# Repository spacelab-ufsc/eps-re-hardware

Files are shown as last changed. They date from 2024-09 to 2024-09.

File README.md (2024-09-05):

<h1 align="center">
	RELIABILITY ENHANCED ELECTRICAL POWER SYSTEM (RE²PS) HARDWARE
	<br>
</h1>

<p align="center">
    
    
    
    
    
    
</p>

<details>
    <summary><b>Summary</b></summary>
    <ol>
        <li>
            <a href="#overview">Overview</a>
        </li>
        <li>
            <a href="#repository-organization">Repository Organization</a>
        </li>
        <li>
            <a href="#license">License</a>
        </li>
        <li>
            <a href="#releases">Releases</a>
        </li>
        <li>
            <a href="#notes">Notes</a>
        </li>
        <li>
            <a href="#references">References</a>
        </li>
    </ol>
</details>

## Overview
The PCB of **RE²PS** [[1]](#1) was designed to be more reliable than previous EPS models developed by SpaceLab. To achieve this, ECSS standards for PCB development in space environments were tailored for the project [[2]](#2). Some flexibility was applied in selecting new connectors for interfacing with other modules, but whenever possible, previously used connectors, such as Pico-Locks and PicoBlades, were chosen.

<!-- 
<p align="center">
    <img src="https://github.com/spacelab-ufsc/eps-re-hardware/blob/main/outputs/eps-re_2D_top.svg" width="400"><img src="https://github.com/spacelab-ufsc/eps-re-hardware/blob/main/outputs/eps-re_2D_bottom.svg" width="400">
</p>
-->

<p align="center">
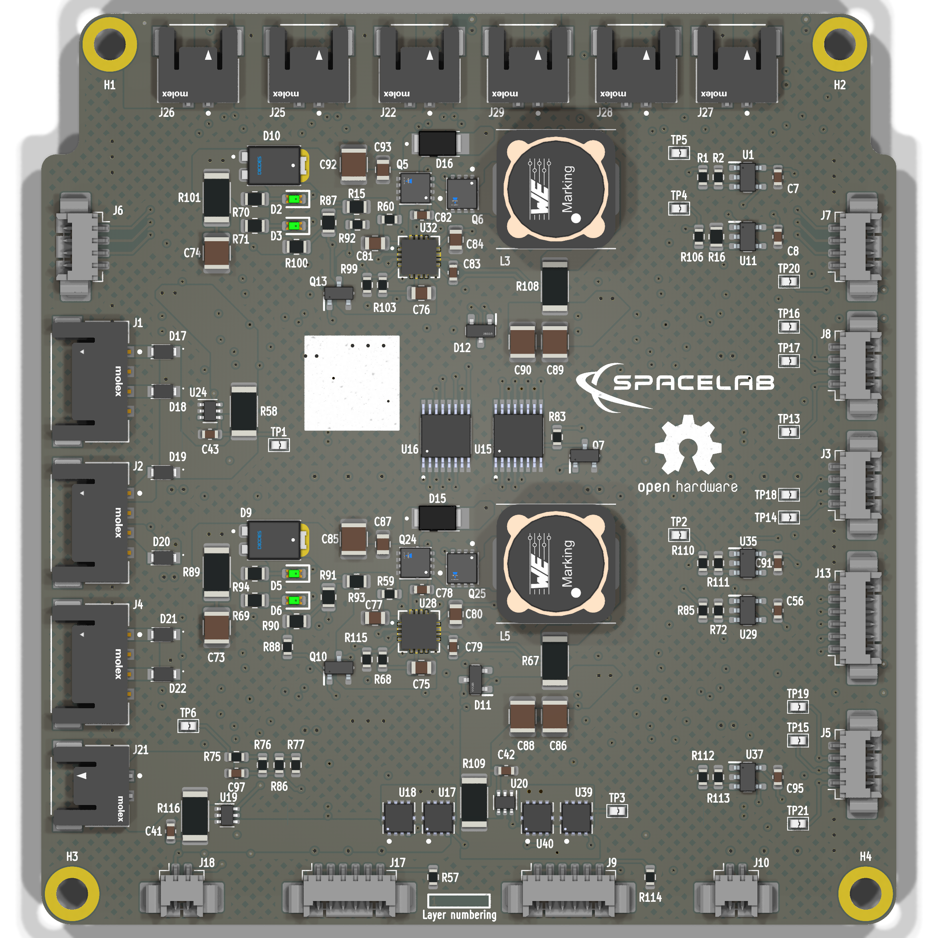
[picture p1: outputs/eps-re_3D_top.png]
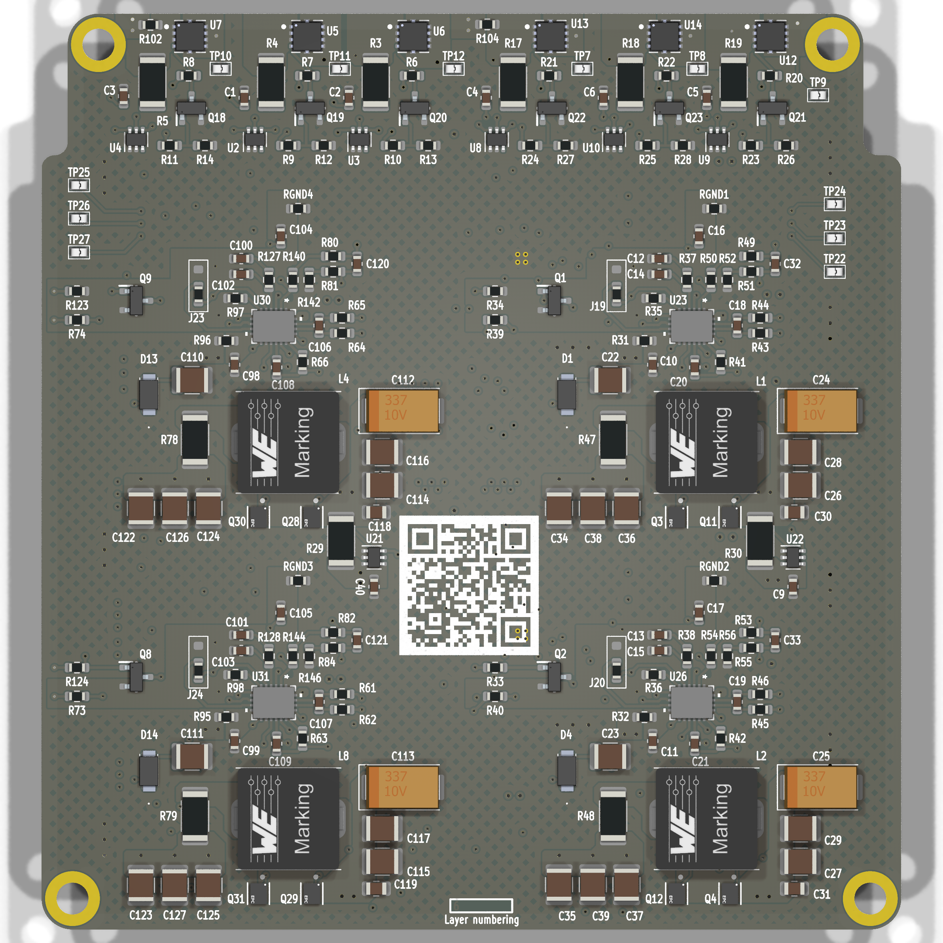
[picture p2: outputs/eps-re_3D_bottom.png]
    
</p>

<p align="center">
    
    
    
</p>

## Repository Organization
`sources`: Main files of the RE²PS's hardware project.

`outputs`: Output files, such as figures of the RE²PS's PCB, schematics, BOM and more.

## License
This project is open-source under the following license: CERN Open Hardware License v2.0.

## Releases

Releases are published after  ensuring that the project itself do not have any major errors and after testing the PCB. Please refer to the **documentation** for more details.

## Notes
For more info about the SpaceLab, access our [GitHub](https://github.com/spacelab-ufsc/spacelab), [Linkedin](https://br.linkedin.com/company/spacelab-ufsc) or our [website](https://spacelab.ufsc.br/en/home/).

## References
<a id="1">[1]</a> D. L. Figueiredo, "Reliability Enhanced Electrical Power System for Nanosatellites," in <i>Repositório Institucional da UFSC</i>, pp. 1-85, 2023, available at <a href="https://repositorio.ufsc.br/bitstream/handle/123456789/247559/PEEL2103-D.pdf?sequence=1&isAllowed=y"> this link</a>.

<a id="2">[2]</a> C. A. Rigo, L. O. Seman, M. D. Berejuck and E. A. Bezerra, "Printed Circuit Board Design Methodology for Embedded Systems Targeting Space Applications," in IEEE Latin America Transactions, vol. 18, no. 02, pp. 257-264, 2020, available at <a href="https://ieeexplore.ieee.org/document/9085278"> this link</a>.

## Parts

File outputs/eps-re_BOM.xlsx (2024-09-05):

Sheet: BOM
 |  |  |  | Project: RE²PS
 |  |  |  | Release: v0.1.0
 |  |  |  | Date: 10/12/2023
 |  |  |  | Responsible: João Cláudio E. B., Gabriel M. M. and Eduardo A. B.
BILL OF MATERIALS (BOM)
Reference | Value | Footprint | Datasheet | MPN | Manufacturer | Observations | Package | Qty | DNP
C1,C2,C3,C4,C5,C6,C7,C8,C9,C10,C11,C20,C21,C40,C41,C42,C43,C56,C78,C79,C82,C83,C91,C95,C98,C99,C108,C109 | 100nF | footprints:CAP0603 | https://br.mouser.com/datasheet/2/447/KEM_C1002_X7R_SMD-3316098.pdf | C0603C104K5RACTU | KEMET |  | SMD 0603 | 28
C12,C13,C100,C101 | 3.3nF | footprints:CAP0603 | https://api.kemet.com/component-edge/download/datasheet/C0603C100J5GACAUTO.pdf | C0603C332J5GACAUTO | KEMET |  | SMD 0603 | 4
C14,C15,C102,C103 | 100pF | footprints:CAP0603 | https://api.kemet.com/component-edge/download/datasheet/C0603C100J5GACAUTO.pdf | C0603C101J5GACAUTO | KEMET |  | SMD 0603 | 4
C16,C17,C18,C19,C104,C105,C106,C107 | 1nF | footprints:CAP0603 | https://api.kemet.com/component-edge/download/datasheet/C0603C100J5GACAUTO.pdf | C0603C102F3GACTU | KEMET |  | SMD 0603 | 8
C22,C23,C110,C111 | 4.7uF | footprints:CAP1210 | https://br.mouser.com/datasheet/2/281/1/GCM32ER71H475KA55_01A-3146523.pdf | GCM32ER71H475KA55L | Murata |  | SMD 1210 | 4
C24,C25,C112,C113 | 47uF | footprints:CAP2917POL | https://content.kemet.com/datasheets/KEM_T2009_T495.pdf | T495X476K035ATE300 | KEMET |  | SMD 2917 | 4
C26,C27,C28,C29,C85,C86,C89,C92,C114,C115,C116,C117 | 10uF | footprints:CAP1210 | https://content.kemet.com/datasheets/KEM_C1002_X7R_SMD.pdf | C1210C106K5RACTU | KEMET |  | SMD 0603 | 12
C30,C31,C75,C76,C77,C80,C81,C84,C87,C93,C118,C119 | 1uF | footprints:CAP0805 | http://www.kemet.com/Lists/ProductCatalog/Attachments/53/KEM_C1002_X7R_SMD.pdf | C0805C105K5RACTU | KEMET |  | SMD 0805 | 12
C32,C33,C97,C120,C121 | 22pF | footprints:CAP0603 | https://api.kemet.com/component-edge/download/datasheet/C0603C100J5GACAUTO.pdf | C0603C220K5RACAUTO | KEMET |  | SMD 0603 | 5
C34,C35,C36,C37,C38,C39,C122,C123,C124,C125,C126,C127 | 22uF | footprints:CAP1210 | https://www.murata.com/en-us/products/productdetail?partno=GCM32ER71C226KE19%23 | GCM32ER71C226KE19L | Murata |  | SMD 1210 | 12
C73,C74 | 2.2uF | footprints:CAP1210 | https://content.kemet.com/datasheets/KEM_C1002_X7R_SMD.pdf | C1210C225K5RACTU | KEMET |  | SMD 1210 | 2
C88,C90 | 4.7uF | footprints:CAP1210 | https://content.kemet.com/datasheets/KEM_C1002_X7R_SMD.pdf | C1210C475K5RACTU | KEMET |  | SMD 1210 | 2
D1,D4,D13,D14 | SS12FP | footprints:SS12FP | http://www.onsemi.com/pub/Collateral/S110FP-D.pdf | SS12FP | onsemi |  | SOD-123HE-2 | 4
D2,D3,D5,D6 | LTST-C190GKT | footprints:LTST-C190GKT | https://media.digikey.com/pdf/Data%20Sheets/Lite-On%20PDFs/LTST-C190GKT.pdf | LTST-C190GKT | Lite-On |  | SMD 0603 | 4
D9,D10 | PDS1040L-13 | footprints:PDS1040L-13 | https://www.diodes.com/assets/Datasheets/ds30486.pdf | PDS1040L-13 | Diode Incorporated |  | PowerDI5-3 | 2
D11,D12 | BAT54 | footprints:BAT54 | https://www.rectron.com/data_sheets/bat54.pdf | BAT54 | Rectron |  | SOT-23 | 2
D15,D16 | PMEG3050EP,115 | footprints:PMEG3050EP,115 | https://assets.nexperia.com/documents/data-sheet/PMEG3050EP.pdf | PMEG3050EP,115 | Nexperia |  | SOD-128-2 | 2
D17,D18,D19,D20,D21,D22 | CUHS20S40,H3F | footprints:CUHS20S40,H3F | https://br.mouser.com/datasheet/2/408/CUHS20S40_datasheet_en_20190925-1505241.pdf | CUHS20S40,H3F | Toshiba |  | SOD-323HE | 6
J1,J2,J4 | 2053380004 | footprints:2053380004 | https://www.molex.com/en-us/products/part-detail/2053380004?display=pdf | 2053380004 | Molex |  | N/A | 3
J3,J5,J6,J7,J8 | 532610471 | footprints:532610471 | https://www.molex.com/en-us/products/part-detail/532610471?display=pdf | 532610471 | Molex |  | N/A | 5
J9,J13,J17 | 532610671 | footprints:532610671 | https://www.molex.com/en-us/products/part-detail/532610671?display=pdf | 532610671 | Molex |  | N/A | 3
J10,J18 | 532610271 | footprints:532610271 | https://www.molex.com/en-us/products/part-detail/532610271?display=pdf | 532610271 | Molex |  | N/A | 2
J21,J22,J25,J26,J27,J28,J29 | 2053380002 | footprints:2053380002 | https://www.molex.com/en-us/products/part-detail/2053380002?display=pdf | 2053380002 | Molex |  | N/A | 7
L1,L2,L4,L8 | 2.4uH | footprints:744325240 | https://www.we-online.com/components/products/datasheet/744325240.pdf | 744325240 | Wurth Elektronik |  | Non-standard | 4
L3,L5 | 12uH | footprints:744770112 | https://www.we-online.com/components/products/datasheet/744770112.pdf | 744770112 | Wurth Elektronik |  | Non-standard | 2
Q1,Q2,Q7,Q8,Q9,Q10,Q13,Q18,Q19,Q20,Q21,Q22,Q23 | SI2302DDS-T1-GE3 | footprints:SI2302DDS-T1-GE3 | http://www.vishay.com/docs/63653/si2302dds.pdf | SI2302DDS-T1-GE3 | Vishay |  | SOT-23-3 | 13
Q3,Q4,Q11,Q12,Q28,Q29,Q30,Q31 | EPC2016C | footprints:EPC2016C | https://epc-co.com/epc/Portals/0/epc/documents/datasheets/EPC2016C_datasheet.pdf | EPC2016C | EPC |  | Non-standard | 8
Q5,Q6,Q24,Q25 | SI7414DN-T1-E3 | footprints:SI7414DN-T1-E3 | http://www.vishay.com/docs/71738/71738.pdf | SI7414DN-T1-E3 | Vishay |  | PowerPAK1212-8 | 4
R1 | 13k | footprints:RES0603 | https://www.vishay.com/docs/20043/crcwhpe3.pdf | CRCW060313K0FKEAHP | Vishay |  | SMD 0603 | 1
R2,R52,R56,R142,R146 | 20k | footprints:RES0603 | https://www.vishay.com/docs/20043/crcwhpe3.pdf | CRCW060320K0FKEAHP | Vishay |  | SMD 0603 | 5
R3,R4,R67,R108 | 33m | footprints:RES2010 | https://www.vishay.com/docs/30100/wsl.pdf | WSL2010R0330FEA | Vishay |  | SMD 2010 | 4
R5 | 18m | footprints:RES2010 | https://www.vishay.com/docs/30100/wsl.pdf | WSL2010R0180FEA | Vishay |  | SMD 2010 | 1
R6,R7,R8,R85 | 30k | footprints:RES0603 | https://www.vishay.com/docs/20043/crcwhpe3.pdf | CRCW060330K0FKEAHP | Vishay |  | SMD 0603 | 4
R9,R10,R11,R23,R24,R25 | 470R | footprints:RES0603 | https://www.vishay.com/docs/20043/crcwhpe3.pdf | CRCW0603470RFKEAHP | Vishay |  | SMD 0603 | 6
R12,R13,R14,R26,R27,R28,R33,R34,R39,R40,R57,R73,R74,R83,R88,R92,R114,R123,R124 | 100k | footprints:RES0603 | https://www.vishay.com/docs/20043/crcwhpe3.pdf | CRCW0603100KFKEAHP | Vishay |  | SMD 0603 | 19
R15,R87,R91,R93 | 20k | footprints:RES0805 | https://www.vishay.com/docs/20043/crcwhpe3.pdf | CRCW080520K0FKEAHP | Vishay |  | SMD 0805 | 4
R16,R69,R70,R71,R94 | 10k | footprints:RES0805 | https://br.mouser.com/datasheet/2/447/YAGEO_PYu_RC_Group_51_RoHS_L_12-3313492.pdf | RC0805FR-0710KL | YAGEO |  | SMD 0805 | 5
R17,R109 | 20m | footprints:RES2010 | https://www.vishay.com/docs/30100/wsl.pdf | WSL2010R0200FEA | Vishay |  | SMD 2010 | 2
R18,R19,R47,R48,R78,R79 | 16m | footprints:RES2010 | https://www.vishay.com/docs/30100/wsl.pdf | WSL2010R0160FEA | Vishay |  | SMD 2010 | 6
R20,R21,R22 | 47k | footprints:RES0603 | https://www.vishay.com/docs/20043/crcwhpe3.pdf | CRCW060347K0FKEAHP | Vishay |  | SMD 0603 | 3
R29,R30 | 5m | footprints:RES2010 | https://www.vishay.com/docs/30100/wsl.pdf | WSL20105L000FEA | Vishay |  | SMD 2010 | 2
R31,R32,R95,R96 | 2.2R | footprints:RES0603 | https://www.vishay.com/docs/20043/crcwhpe3.pdf | CRCW06032R20FKEAHP | Vishay |  | SMD 0603 | 4
R35,R36,R97,R98 | 82k | footprints:RES0603 | https://www.vishay.com/docs/20035/dcrcwe3.pdf | CRCW060382K0FKEA | Vishay |  | SMD 0603 | 4
R37,R38,R127,R128 | 12k | footprints:RES0603 | https://www.vishay.com/docs/20043/crcwhpe3.pdf | CRCW060312K0FKEAHP | Vishay |  | SMD 0603 | 4
R41,R42,R43,R44,R45,R46,R59,R60,R61,R62,R63,R64,R65,R66 | 10R | footprints:RES0603 | https://www.vishay.com/docs/20043/crcwhpe3.pdf | CRCW060310R0FKEAHP | Vishay |  | SMD 0603 | 14
R49,R51,R53,R55,R76,R77,R80,R81,R82,R84,R102,R104,RGND1,RGND2,RGND3,RGND4 | 0R | footprints:RES0603 | https://www.vishay.com/docs/20043/crcwhpe3.pdf | CRCW06030000Z0EAHP | Vishay |  | SMD 0603 | 16
R50,R54 | 150k | footprints:RES0603 | https://www.vishay.com/docs/20043/crcwhpe3.pdf | CRCW0603150KFKEAHP | Vishay |  | SMD 0603 | 2
R58 | 25m | footprints:RES2010 | https://www.vishay.com/docs/31057/wslhigh.pdf | WSL2010R0250FEA18 | Vishay |  | SMD 2010 | 1
R68,R103 | 5.23k | footprints:RES0603 | https://www.vishay.com/docs/20043/crcwhpe3.pdf | CRCW06035K23FKEAHP | Vishay |  | SMD 0603 | 2
R72 | 8.2k | footprints:RES0603 | https://www.vishay.com/docs/20043/crcwhpe3.pdf | CRCW06038K20FKEAHP | Vishay |  | SMD 0603 | 1
R75 | 110k | footprints:RES0603 | https://www.vishay.com/docs/20043/crcwhpe3.pdf | CRCW0603110KFKEAHP | Vishay |  | SMD 0603 | 1
R86 | 37.4k | footprints:RES0603 | https://www.vishay.com/docs/20043/crcwhpe3.pdf | CRCW060337K4FKEAHP | Vishay |  | SMD 0603 | 1
R89,R101 | 2R | footprints:RES2010 | https://www.vishay.com/docs/20035/dcrcwe3.pdf | CRCW20102R00FKEF | Vishay |  | SMD 2010 | 2
R90,R100 | 270k | footprints:RES0805 | https://www.vishay.com/docs/20043/crcwhpe3.pdf | CRCW0805270KFKEAHP | Vishay |  | SMD 0805 | 2
R99,R115 | 30.1k | footprints:RES0603 | https://www.vishay.com/docs/20043/crcwhpe3.pdf | CRCW060330K1FKEAHP | Vishay |  | SMD 0603 | 2
R106 | 15k | footprints:RES0603 | https://www.vishay.com/docs/20043/crcwhpe3.pdf | CRCW060315K0FKEAHP | Vishay |  | SMD 0603 | 1
R110,R112 | 24k | footprints:RES0603 | https://www.vishay.com/docs/20043/crcwhpe3.pdf | CRCW060324K0FKEAHP | Vishay |  | SMD 0603 | 2
R111,R113 | 7.5k | footprints:RES0603 | https://www.vishay.com/docs/20043/crcwhpe3.pdf | CRCW06037K50FKEAHP | Vishay |  | SMD 0603 | 2
R116 | 8m | footprints:RES2010 | https://www.vishay.com/docs/31057/wslhigh.pdf | WSL20108L000FEA18 | Vishay |  | SMD 2010 | 1
R140,R144 | 90.9k | footprints:RES0603 | https://www.vishay.com/docs/20043/crcwhpe3.pdf | CRCW060390K9FKEAHP | Vishay |  | SMD 0603 | 2
TP1,TP2,TP3,TP4,TP5,TP6,TP7,TP8,TP9,TP10,TP11,TP12,TP13,TP14,TP15,TP16,TP17,TP18,TP19,TP20,TP21,TP22,TP23,TP24,TP25,TP26,TP27 | Test point | footprints:testpoint_smd | https://br.mouser.com/datasheet/2/181/S2761R-1291319.pdf | S2761-46R | Harwin |  | Non-standard | 27
U1,U11,U29,U35,U37 | LMV321RIYLT | footprints:LMV321RIYLT | https://br.mouser.com/datasheet/2/389/lmv321-1849557.pdf | LMV321RIYLT | STMicroelectronics |  | SOT-23-5 | 5
U2,U3,U9,U10,U19,U21,U22 | INA199C3DCKR | footprints:INA199C3DCKR | https://www.ti.com/lit/ds/symlink/ina199.pdf?HQS=dis-mous-null-mousermode-dsf-pf-null-wwe&ts=1699134415152 | INA199C3DCKR | TI |  | SC70-6 | 7
U4,U8,U20,U24 | INA199C1DCKR | footprints:INA199C1DCKR | https://www.ti.com/lit/ds/symlink/ina199.pdf?ts=1720820884105 | INA199C1DCKR | Texas Instruments |  | SC70-6 | 4
U5,U6,U7,U12,U13,U14,U17,U18,U39,U40 | NVTFS5116PLTAG | footprints:NVTFS5116PLTAG | https://br.mouser.com/datasheet/2/308/1/NVTFS5116PL_D-2319932.pdf | NVTFS5116PLTAG | onsemi |  | WDFN-8 | 10
U15,U16 | CD4051BPWR | footprints:CD4051BPWR | https://www.ti.com/lit/ds/symlink/cd4051b.pdf?ts=1685905129974 | CD4051BPWR | TI |  | TSSOP-16 | 2
U23,U26,U30,U31 | LTC3833EUDC#TRPBF | footprints:LTC3833EUDC#TRPBF | https://www.analog.com/media/en/technical-documentation/data-sheets/3833f.pdf | LTC3833EUDC#TRPBF | Analog Devices |  | QFN-20 | 4
U28,U32 | BQ24650RVAT | footprints:BQ24650RVAT | https://www.ti.com/general/docs/suppproductinfo.tsp?distId=26&gotoUrl=https://www.ti.com/lit/gpn/bq24650 | BQ24650RVAT | TI |  | VQFN-16 | 2

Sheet: csv
C1,C2,C3,C4,C5,C6,C7,C8,C9,C10,C11,C20,C21,C40,C41,C42,C43,C56,C78,C79,C82,C83,C91,C95,C98,C99,C108,C109 | 100nF | footprints:CAP0603 | https://br.mouser.com/datasheet/2/447/KEM_C1002_X7R_SMD-3316098.pdf | C0603C104K5RACTU | KEMET | SMD 0603 | 28
C12,C13,C100,C101 | 3.3nF | footprints:CAP0603 | https://api.kemet.com/component-edge/download/datasheet/C0603C100J5GACAUTO.pdf | C0603C332J5GACAUTO | KEMET | SMD 0603 | 4
C14,C15,C102,C103 | 100pF | footprints:CAP0603 | https://api.kemet.com/component-edge/download/datasheet/C0603C100J5GACAUTO.pdf | C0603C101J5GACAUTO | KEMET | SMD 0603 | 4
C16,C17,C18,C19,C104,C105,C106,C107 | 1nF | footprints:CAP0603 | https://api.kemet.com/component-edge/download/datasheet/C0603C100J5GACAUTO.pdf | C0603C102F3GACTU | KEMET | SMD 0603 | 8
C22,C23,C110,C111 | 4.7uF | footprints:CAP1210 | https://br.mouser.com/datasheet/2/281/1/GCM32ER71H475KA55_01A-3146523.pdf | GCM32ER71H475KA55L | Murata | SMD 1210 | 4
C24,C25,C112,C113 | 47uF | footprints:CAP2917POL | https://content.kemet.com/datasheets/KEM_T2009_T495.pdf | T495X476K035ATE300 | KEMET | SMD 2917 | 4
C26,C27,C28,C29,C85,C86,C89,C92,C114,C115,C116,C117 | 10uF | footprints:CAP1210 | https://content.kemet.com/datasheets/KEM_C1002_X7R_SMD.pdf | C1210C106K5RACTU | KEMET | SMD 0603 | 12
C30,C31,C75,C76,C77,C80,C81,C84,C87,C93,C118,C119 | 1uF | footprints:CAP0805 | http://www.kemet.com/Lists/ProductCatalog/Attachments/53/KEM_C1002_X7R_SMD.pdf | C0805C105K5RACTU | KEMET | SMD 0805 | 12
C32,C33,C97,C120,C121 | 22pF | footprints:CAP0603 | https://api.kemet.com/component-edge/download/datasheet/C0603C100J5GACAUTO.pdf | C0603C220K5RACAUTO | KEMET | SMD 0603 | 5
C34,C35,C36,C37,C38,C39,C122,C123,C124,C125,C126,C127 | 22uF | footprints:CAP1210 | https://www.murata.com/en-us/products/productdetail?partno=GCM32ER71C226KE19%23 | GCM32ER71C226KE19L | Murata | SMD 1210 | 12
C73,C74 | 2.2uF | footprints:CAP1210 | https://content.kemet.com/datasheets/KEM_C1002_X7R_SMD.pdf | C1210C225K5RACTU | KEMET | SMD 1210 | 2
C88,C90 | 4.7uF | footprints:CAP1210 | https://content.kemet.com/datasheets/KEM_C1002_X7R_SMD.pdf | C1210C475K5RACTU | KEMET | SMD 1210 | 2
D1,D4,D13,D14 | SS12FP | footprints:SS12FP | http://www.onsemi.com/pub/Collateral/S110FP-D.pdf | SS12FP | onsemi | SOD-123HE-2 | 4
D2,D3,D5,D6 | LTST-C190GKT | footprints:LTST-C190GKT | https://media.digikey.com/pdf/Data%20Sheets/Lite-On%20PDFs/LTST-C190GKT.pdf | LTST-C190GKT | Lite-On | SMD 0603 | 4
D9,D10 | PDS1040L-13 | footprints:PDS1040L-13 | https://www.diodes.com/assets/Datasheets/ds30486.pdf | PDS1040L-13 | Diode Incorporated | PowerDI5-3 | 2
D11,D12 | BAT54 | footprints:BAT54 | https://www.rectron.com/data_sheets/bat54.pdf | BAT54 | Rectron | SOT-23 | 2
D15,D16 | PMEG3050EP,115 | footprints:PMEG3050EP,115 | https://assets.nexperia.com/documents/data-sheet/PMEG3050EP.pdf | PMEG3050EP,115 | Nexperia | SOD-128-2 | 2
D17,D18,D19,D20,D21,D22 | CUHS20S40,H3F | footprints:CUHS20S40,H3F | https://br.mouser.com/datasheet/2/408/CUHS20S40_datasheet_en_20190925-1505241.pdf | CUHS20S40,H3F | Toshiba | SOD-323HE | 6
J1,J2,J4 | 2053380004 | footprints:2053380004 | https://www.molex.com/en-us/products/part-detail/2053380004?display=pdf | 2053380004 | Molex | N/A | 3
J3,J5,J6,J7,J8 | 532610471 | footprints:532610471 | https://www.molex.com/en-us/products/part-detail/532610471?display=pdf | 532610471 | Molex | N/A | 5
J9,J13,J17 | 532610671 | footprints:532610671 | https://www.molex.com/en-us/products/part-detail/532610671?display=pdf | 532610671 | Molex | N/A | 3
J10,J18 | 532610271 | footprints:532610271 | https://www.molex.com/en-us/products/part-detail/532610271?display=pdf | 532610271 | Molex | N/A | 2
J21,J22,J25,J26,J27,J28,J29 | 2053380002 | footprints:2053380002 | https://www.molex.com/en-us/products/part-detail/2053380002?display=pdf | 2053380002 | Molex | N/A | 7
L1,L2,L4,L8 | 2.4uH | footprints:744325240 | https://www.we-online.com/components/products/datasheet/744325240.pdf | 744325240 | Wurth Elektronik | Non-standard | 4
L3,L5 | 12uH | footprints:744770112 | https://www.we-online.com/components/products/datasheet/744770112.pdf | 744770112 | Wurth Elektronik | Non-standard | 2
Q1,Q2,Q7,Q8,Q9,Q10,Q13,Q18,Q19,Q20,Q21,Q22,Q23 | SI2302DDS-T1-GE3 | footprints:SI2302DDS-T1-GE3 | http://www.vishay.com/docs/63653/si2302dds.pdf | SI2302DDS-T1-GE3 | Vishay | SOT-23-3 | 13
Q3,Q4,Q11,Q12,Q28,Q29,Q30,Q31 | EPC2016C | footprints:EPC2016C | https://epc-co.com/epc/Portals/0/epc/documents/datasheets/EPC2016C_datasheet.pdf | EPC2016C | EPC | Non-standard | 8
Q5,Q6,Q24,Q25 | SI7414DN-T1-E3 | footprints:SI7414DN-T1-E3 | http://www.vishay.com/docs/71738/71738.pdf | SI7414DN-T1-E3 | Vishay | PowerPAK1212-8 | 4
R1 | 13k | footprints:RES0603 | https://www.vishay.com/docs/20043/crcwhpe3.pdf | CRCW060313K0FKEAHP | Vishay | SMD 0603 | 1
R2,R52,R56,R142,R146 | 20k | footprints:RES0603 | https://www.vishay.com/docs/20043/crcwhpe3.pdf | CRCW060320K0FKEAHP | Vishay | SMD 0603 | 5
R3,R4,R67,R108 | 33m | footprints:RES2010 | https://www.vishay.com/docs/30100/wsl.pdf | WSL2010R0330FEA | Vishay | SMD 2010 | 4
R5 | 18m | footprints:RES2010 | https://www.vishay.com/docs/30100/wsl.pdf | WSL2010R0180FEA | Vishay | SMD 2010 | 1
R6,R7,R8,R85 | 30k | footprints:RES0603 | https://www.vishay.com/docs/20043/crcwhpe3.pdf | CRCW060330K0FKEAHP | Vishay | SMD 0603 | 4
R9,R10,R11,R23,R24,R25 | 470R | footprints:RES0603 | https://www.vishay.com/docs/20043/crcwhpe3.pdf | CRCW0603470RFKEAHP | Vishay | SMD 0603 | 6
R12,R13,R14,R26,R27,R28,R33,R34,R39,R40,R57,R73,R74,R83,R88,R92,R114,R123,R124 | 100k | footprints:RES0603 | https://www.vishay.com/docs/20043/crcwhpe3.pdf | CRCW0603100KFKEAHP | Vishay | SMD 0603 | 19
R15,R87,R91,R93 | 20k | footprints:RES0805 | https://www.vishay.com/docs/20043/crcwhpe3.pdf | CRCW080520K0FKEAHP | Vishay | SMD 0805 | 4
R16,R69,R70,R71,R94 | 10k | footprints:RES0805 | https://br.mouser.com/datasheet/2/447/YAGEO_PYu_RC_Group_51_RoHS_L_12-3313492.pdf | RC0805FR-0710KL | YAGEO | SMD 0805 | 5
R17,R109 | 20m | footprints:RES2010 | https://www.vishay.com/docs/30100/wsl.pdf | WSL2010R0200FEA | Vishay | SMD 2010 | 2
R18,R19,R47,R48,R78,R79 | 16m | footprints:RES2010 | https://www.vishay.com/docs/30100/wsl.pdf | WSL2010R0160FEA | Vishay | SMD 2010 | 6
R20,R21,R22 | 47k | footprints:RES0603 | https://www.vishay.com/docs/20043/crcwhpe3.pdf | CRCW060347K0FKEAHP | Vishay | SMD 0603 | 3
R29,R30 | 5m | footprints:RES2010 | https://www.vishay.com/docs/30100/wsl.pdf | WSL20105L000FEA | Vishay | SMD 2010 | 2
R31,R32,R95,R96 | 2.2R | footprints:RES0603 | https://www.vishay.com/docs/20043/crcwhpe3.pdf | CRCW06032R20FKEAHP | Vishay | SMD 0603 | 4
R35,R36,R97,R98 | 82k | footprints:RES0603 | https://www.vishay.com/docs/20035/dcrcwe3.pdf | CRCW060382K0FKEA | Vishay | SMD 0603 | 4
R37,R38,R127,R128 | 12k | footprints:RES0603 | https://www.vishay.com/docs/20043/crcwhpe3.pdf | CRCW060312K0FKEAHP | Vishay | SMD 0603 | 4
R41,R42,R43,R44,R45,R46,R59,R60,R61,R62,R63,R64,R65,R66 | 10R | footprints:RES0603 | https://www.vishay.com/docs/20043/crcwhpe3.pdf | CRCW060310R0FKEAHP | Vishay | SMD 0603 | 14
R49,R51,R53,R55,R76,R77,R80,R81,R82,R84,R102,R104,RGND1,RGND2,RGND3,RGND4 | 0R | footprints:RES0603 | https://www.vishay.com/docs/20043/crcwhpe3.pdf | CRCW06030000Z0EAHP | Vishay | SMD 0603 | 16
R50,R54 | 150k | footprints:RES0603 | https://www.vishay.com/docs/20043/crcwhpe3.pdf | CRCW0603150KFKEAHP | Vishay | SMD 0603 | 2
R58 | 25m | footprints:RES2010 | https://www.vishay.com/docs/31057/wslhigh.pdf | WSL2010R0250FEA18 | Vishay | SMD 2010 | 1
R68,R103 | 5.23k | footprints:RES0603 | https://www.vishay.com/docs/20043/crcwhpe3.pdf | CRCW06035K23FKEAHP | Vishay | SMD 0603 | 2
R72 | 8.2k | footprints:RES0603 | https://www.vishay.com/docs/20043/crcwhpe3.pdf | CRCW06038K20FKEAHP | Vishay | SMD 0603 | 1
R75 | 110k | footprints:RES0603 | https://www.vishay.com/docs/20043/crcwhpe3.pdf | CRCW0603110KFKEAHP | Vishay | SMD 0603 | 1
R86 | 37.4k | footprints:RES0603 | https://www.vishay.com/docs/20043/crcwhpe3.pdf | CRCW060337K4FKEAHP | Vishay | SMD 0603 | 1
R89,R101 | 2R | footprints:RES2010 | https://www.vishay.com/docs/20035/dcrcwe3.pdf | CRCW20102R00FKEF | Vishay | SMD 2010 | 2
R90,R100 | 270k | footprints:RES0805 | https://www.vishay.com/docs/20043/crcwhpe3.pdf | CRCW0805270KFKEAHP | Vishay | SMD 0805 | 2
R99,R115 | 30.1k | footprints:RES0603 | https://www.vishay.com/docs/20043/crcwhpe3.pdf | CRCW060330K1FKEAHP | Vishay | SMD 0603 | 2
R106 | 15k | footprints:RES0603 | https://www.vishay.com/docs/20043/crcwhpe3.pdf | CRCW060315K0FKEAHP | Vishay | SMD 0603 | 1
R110,R112 | 24k | footprints:RES0603 | https://www.vishay.com/docs/20043/crcwhpe3.pdf | CRCW060324K0FKEAHP | Vishay | SMD 0603 | 2
R111,R113 | 7.5k | footprints:RES0603 | https://www.vishay.com/docs/20043/crcwhpe3.pdf | CRCW06037K50FKEAHP | Vishay | SMD 0603 | 2
R116 | 8m | footprints:RES2010 | https://www.vishay.com/docs/31057/wslhigh.pdf | WSL20108L000FEA18 | Vishay | SMD 2010 | 1
R140,R144 | 90.9k | footprints:RES0603 | https://www.vishay.com/docs/20043/crcwhpe3.pdf | CRCW060390K9FKEAHP | Vishay | SMD 0603 | 2
TP1,TP2,TP3,TP4,TP5,TP6,TP7,TP8,TP9,TP10,TP11,TP12,TP13,TP14,TP15,TP16,TP17,TP18,TP19,TP20,TP21,TP22,TP23,TP24,TP25,TP26,TP27 | Test point | footprints:testpoint_smd | https://br.mouser.com/datasheet/2/181/S2761R-1291319.pdf | S2761-46R | Harwin | Non-standard | 27
U1,U11,U29,U35,U37 | LMV321RIYLT | footprints:LMV321RIYLT | https://br.mouser.com/datasheet/2/389/lmv321-1849557.pdf | LMV321RIYLT | STMicroelectronics | SOT-23-5 | 5
U2,U3,U9,U10,U19,U21,U22 | INA199C3DCKR | footprints:INA199C3DCKR | https://www.ti.com/lit/ds/symlink/ina199.pdf?HQS=dis-mous-null-mousermode-dsf-pf-null-wwe&ts=1699134415152 | INA199C3DCKR | TI | SC70-6 | 7
U4,U8,U20,U24 | INA199C1DCKR | footprints:INA199C1DCKR | https://www.ti.com/lit/ds/symlink/ina199.pdf?ts=1720820884105 | INA199C1DCKR | Texas Instruments | SC70-6 | 4
U5,U6,U7,U12,U13,U14,U17,U18,U39,U40 | NVTFS5116PLTAG | footprints:NVTFS5116PLTAG | https://br.mouser.com/datasheet/2/308/1/NVTFS5116PL_D-2319932.pdf | NVTFS5116PLTAG | onsemi | WDFN-8 | 10
U15,U16 | CD4051BPWR | footprints:CD4051BPWR | https://www.ti.com/lit/ds/symlink/cd4051b.pdf?ts=1685905129974 | CD4051BPWR | TI | TSSOP-16 | 2
U23,U26,U30,U31 | LTC3833EUDC#TRPBF | footprints:LTC3833EUDC#TRPBF | https://www.analog.com/media/en/technical-documentation/data-sheets/3833f.pdf | LTC3833EUDC#TRPBF | Analog Devices | QFN-20 | 4
U28,U32 | BQ24650RVAT | footprints:BQ24650RVAT | https://www.ti.com/general/docs/suppproductinfo.tsp?distId=26&gotoUrl=https://www.ti.com/lit/gpn/bq24650 | BQ24650RVAT | TI | VQFN-16 | 2

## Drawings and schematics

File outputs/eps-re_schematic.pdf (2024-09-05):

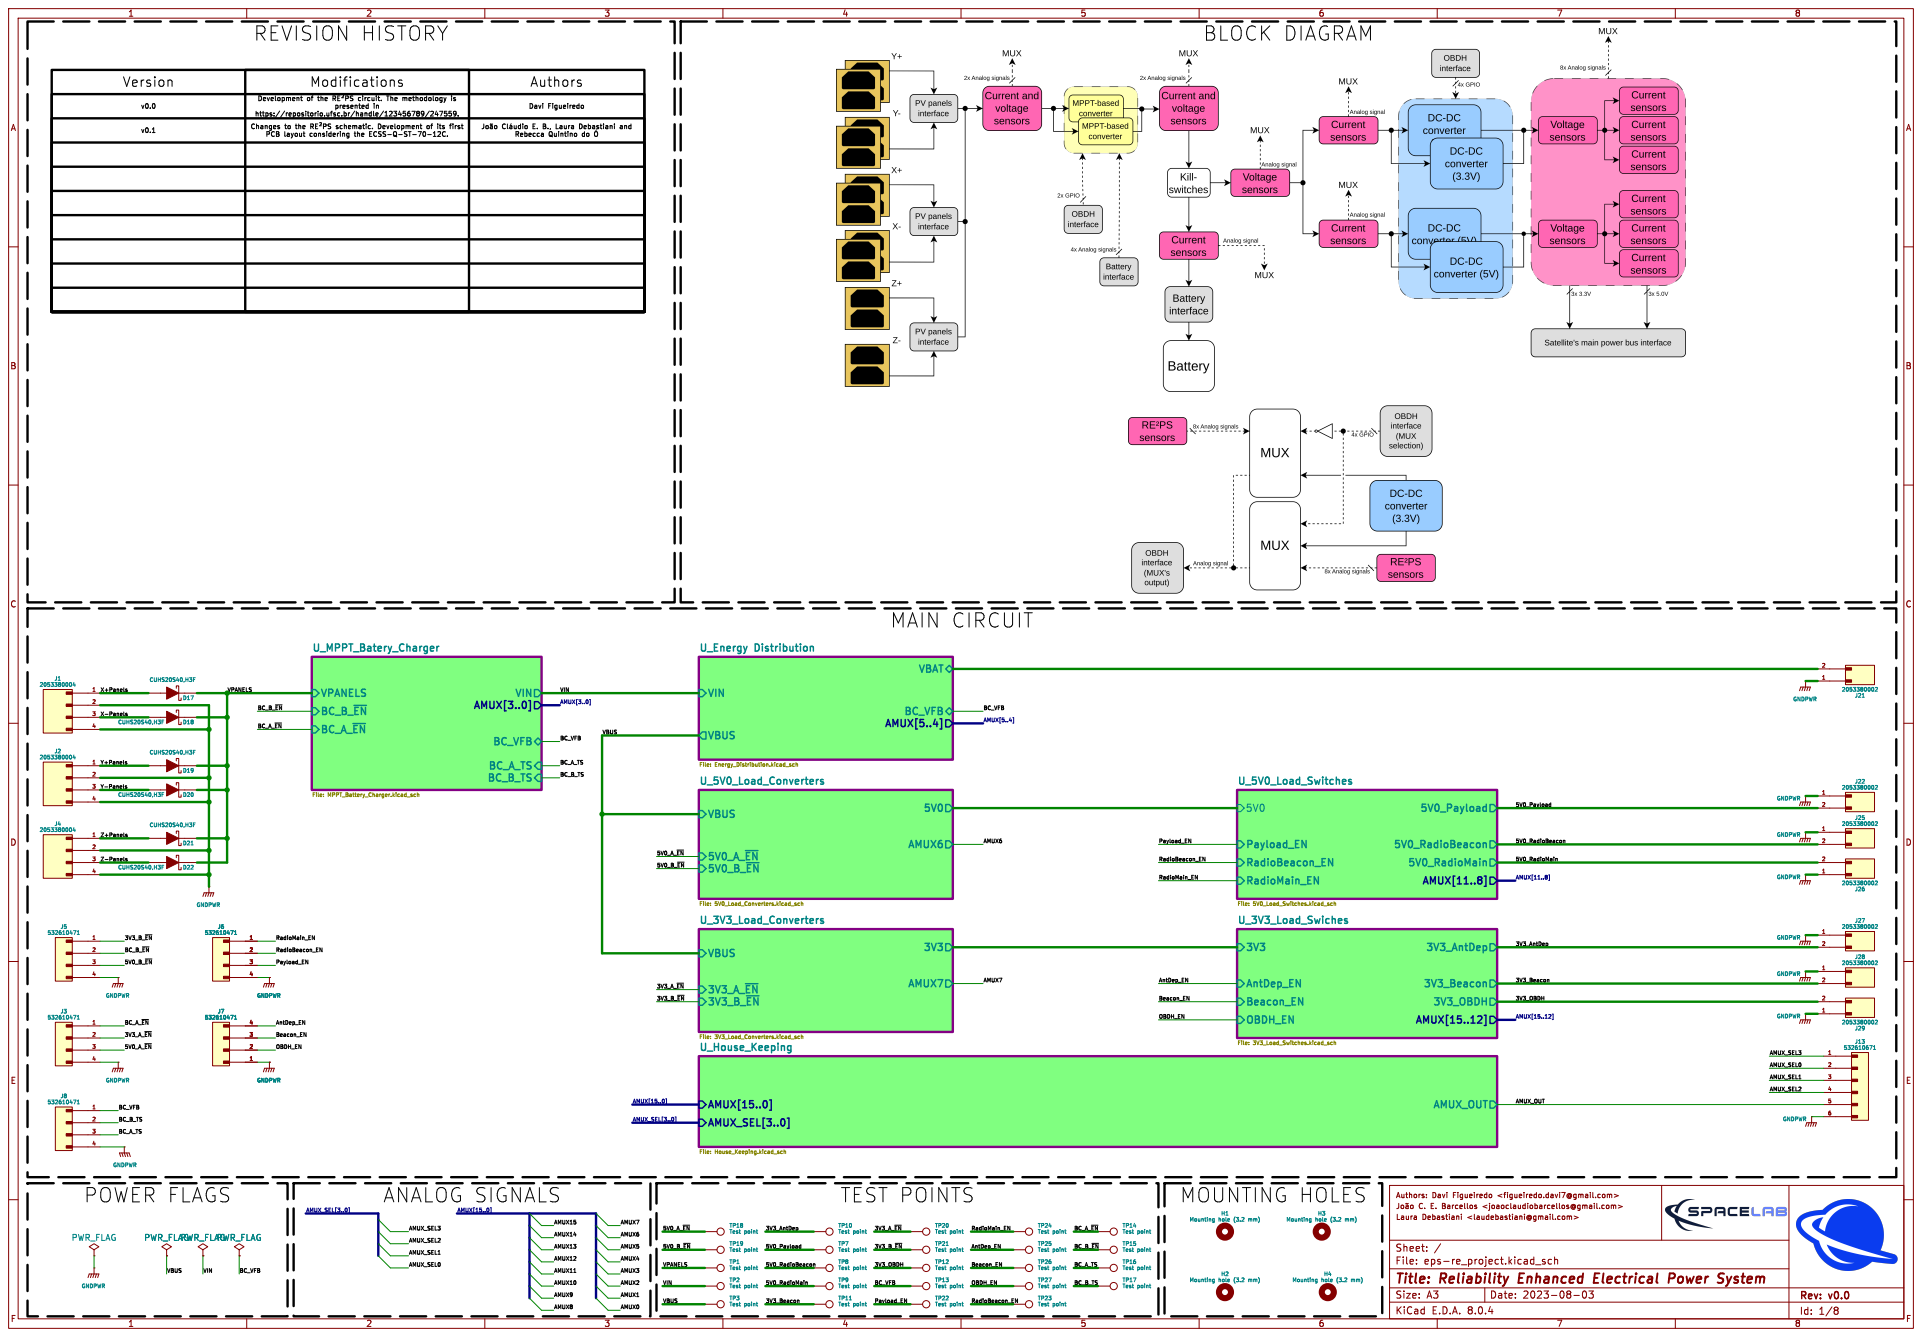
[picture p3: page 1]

https://repositorio.ufsc.br/handle/123456789/247559. Version

Development of the þÿRE²PScircuit. The methodology is presented in

þÿJoãoþÿCláudio E. B., Laura Debastiani and Rebecca Quintino do þÿÓ

TP20 Test point TP21 Test point

Id: 1/8 Title: Reliability Enhanced Electrical Power System

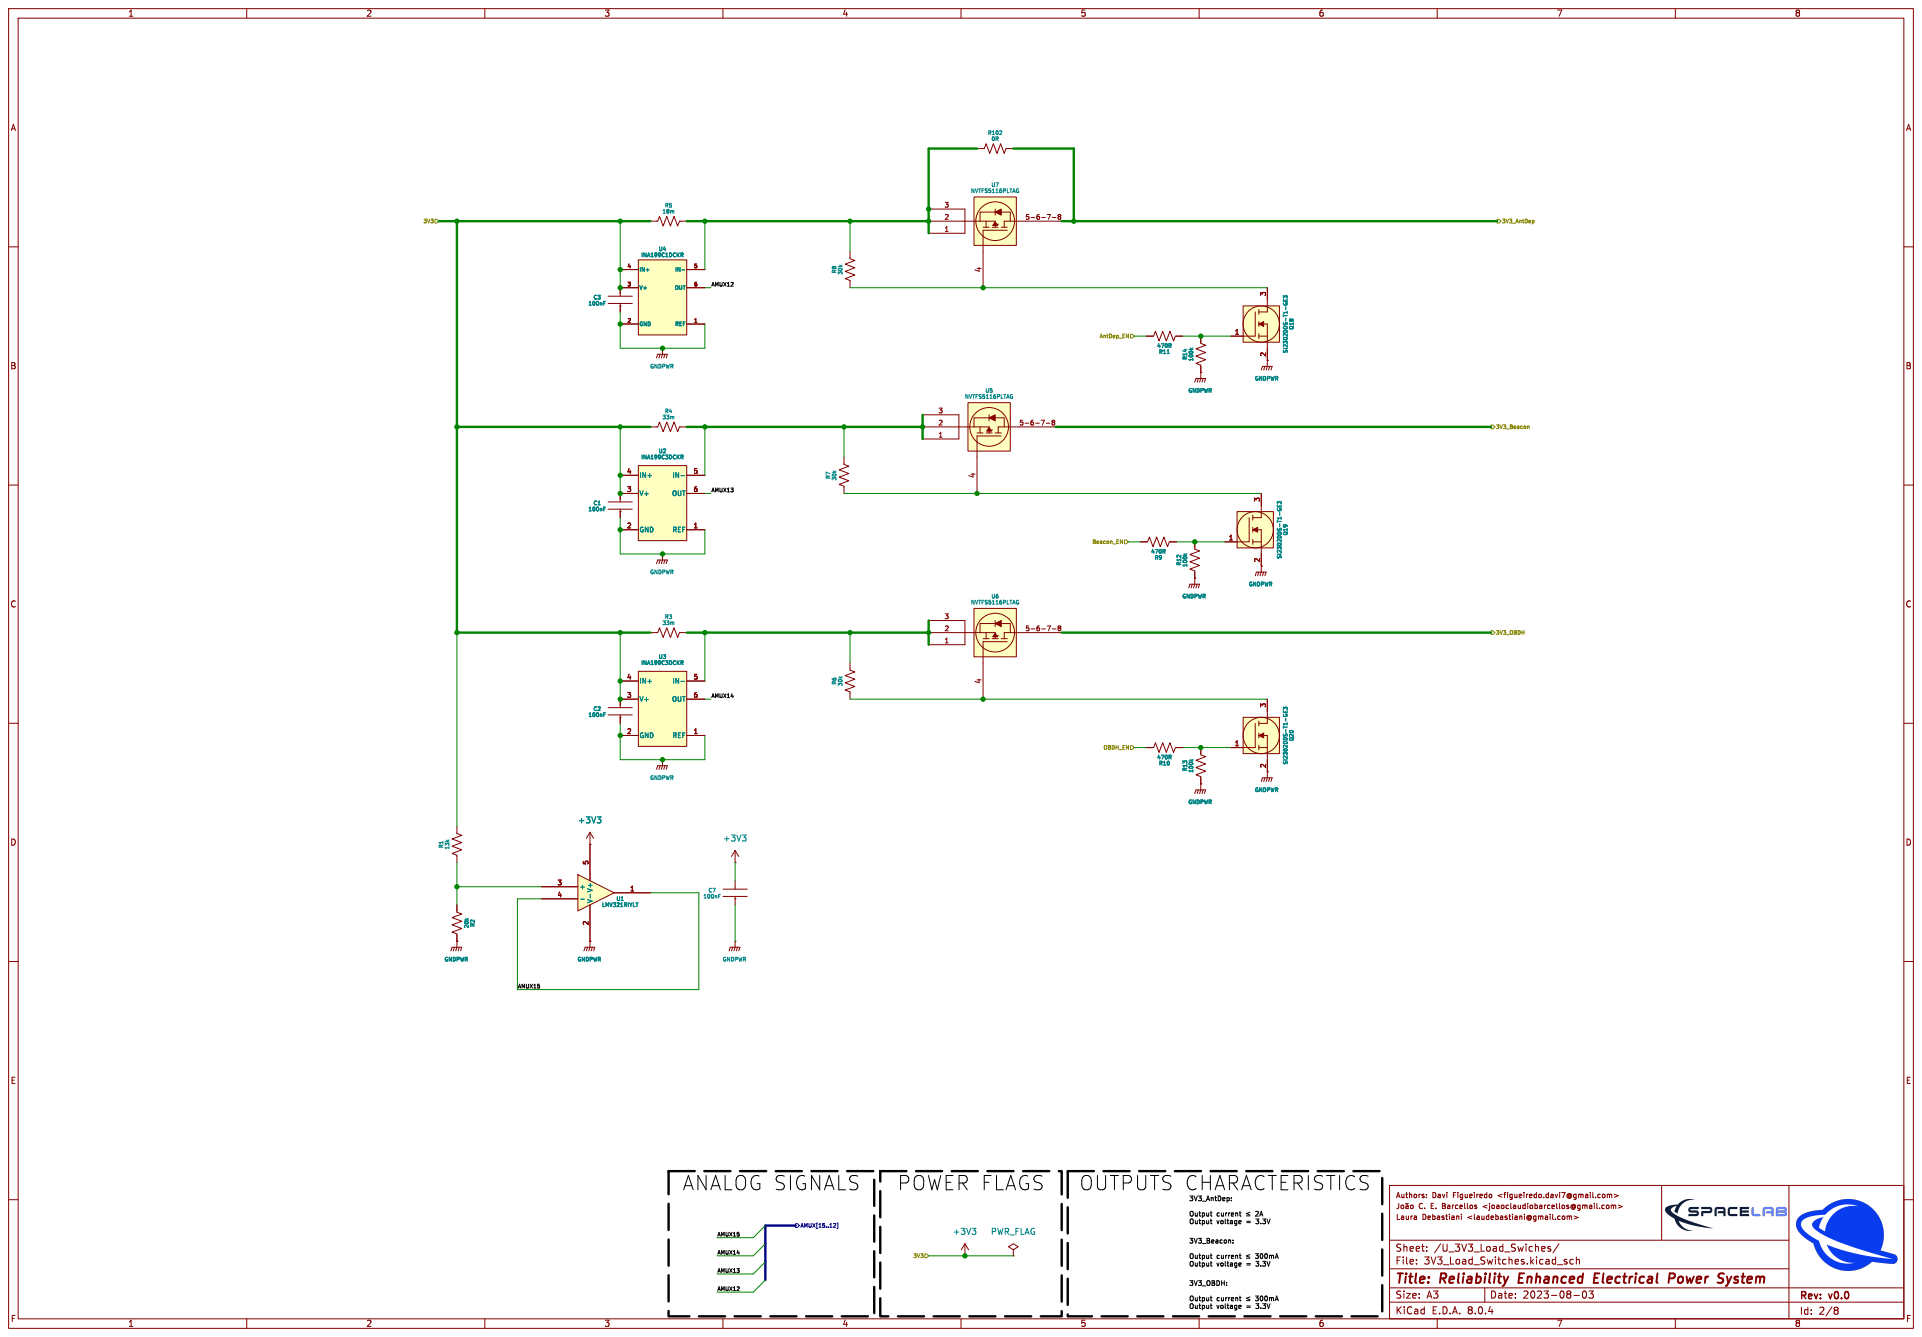
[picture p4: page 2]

2 3 Q20 SI2302DDS-T1-GE3 GNDPWR GNDPWR REF 1 GND 2 V+ 3

Id: 2/8 Title: Reliability Enhanced Electrical Power System

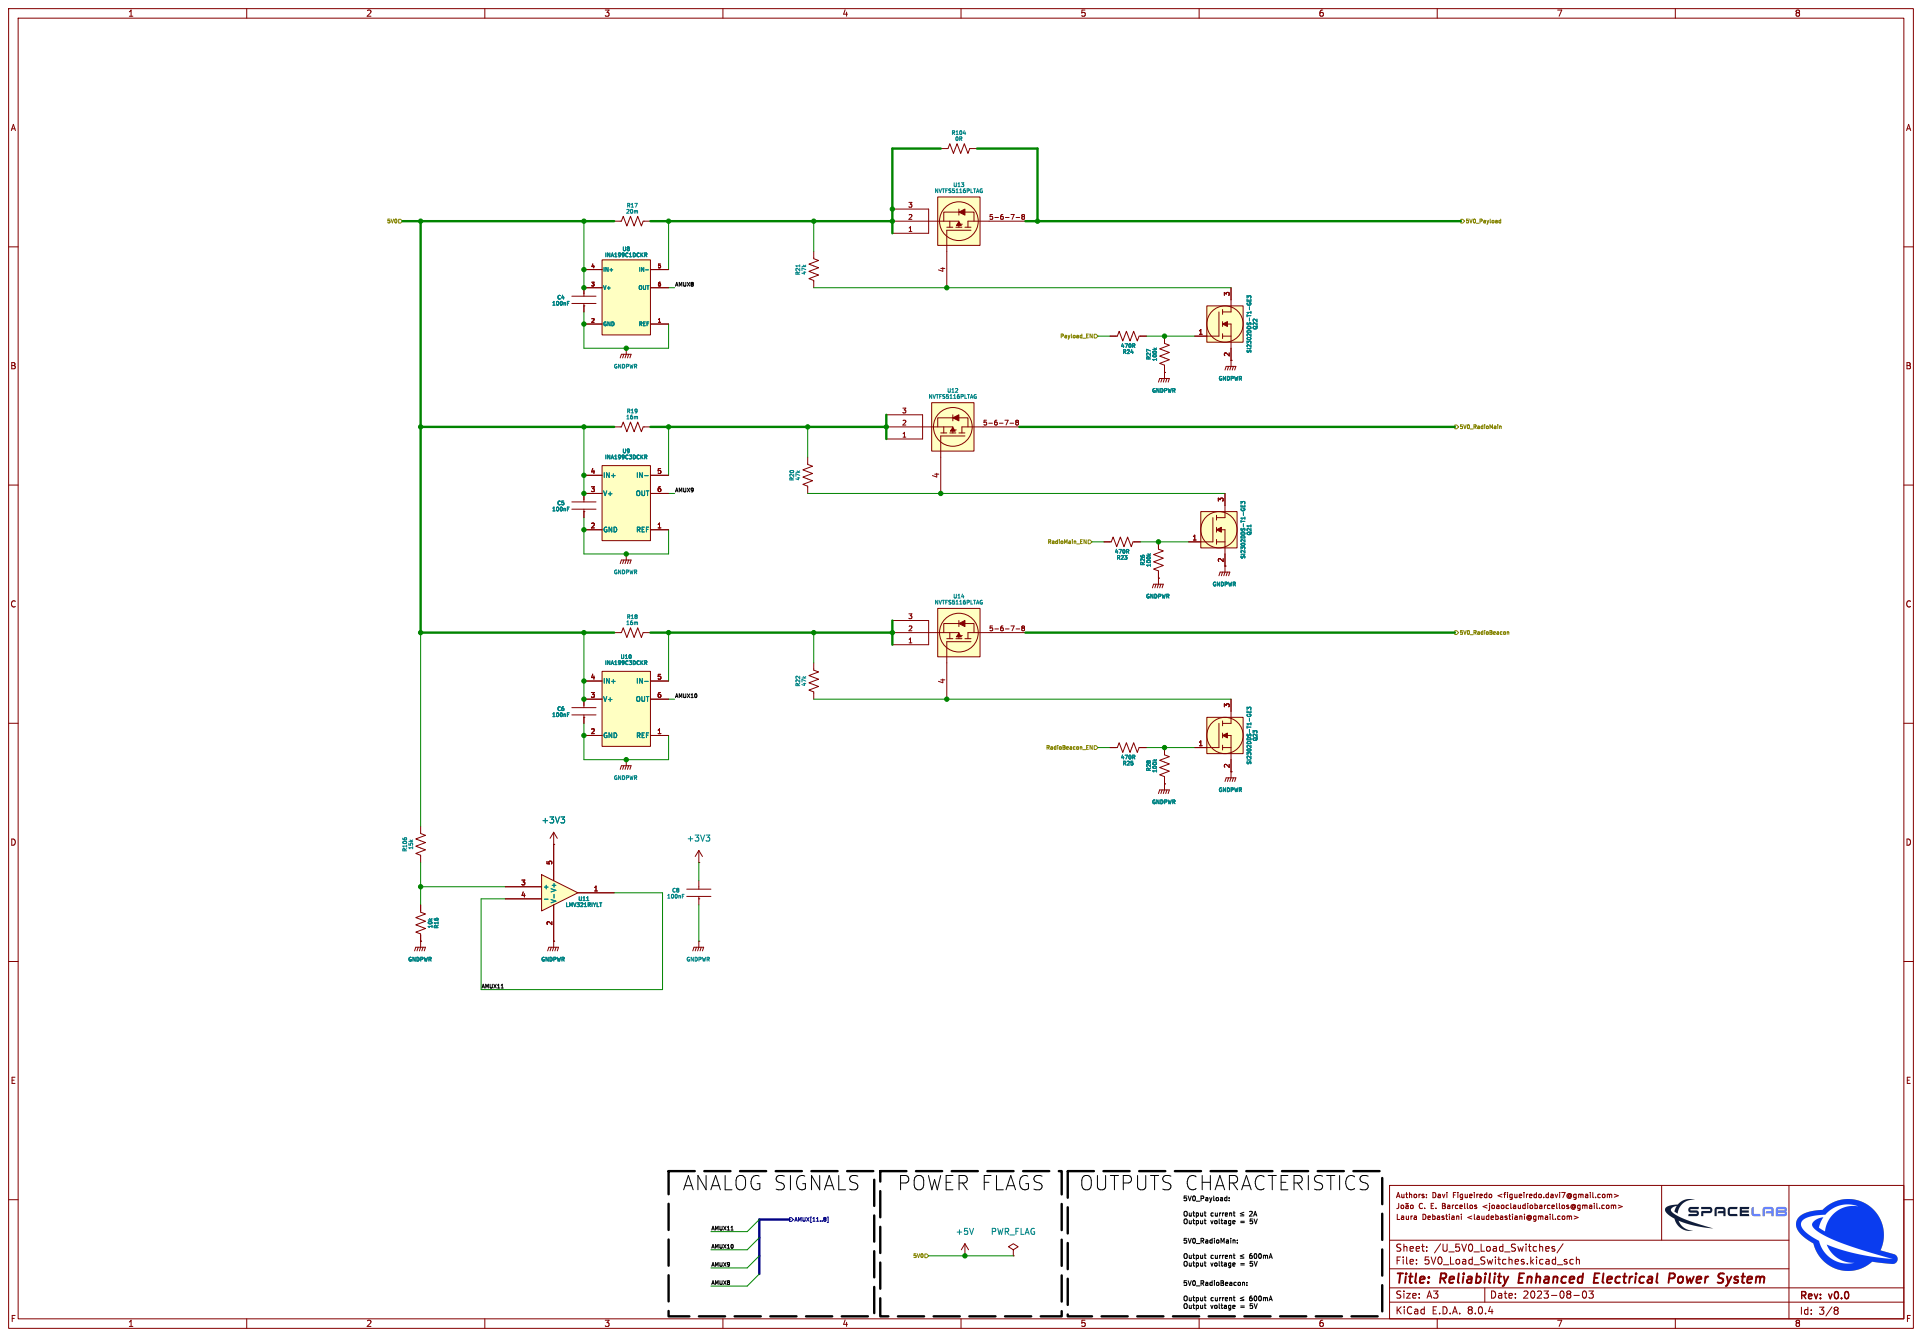
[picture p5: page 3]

Id: 3/8 Title: Reliability Enhanced Electrical Power System

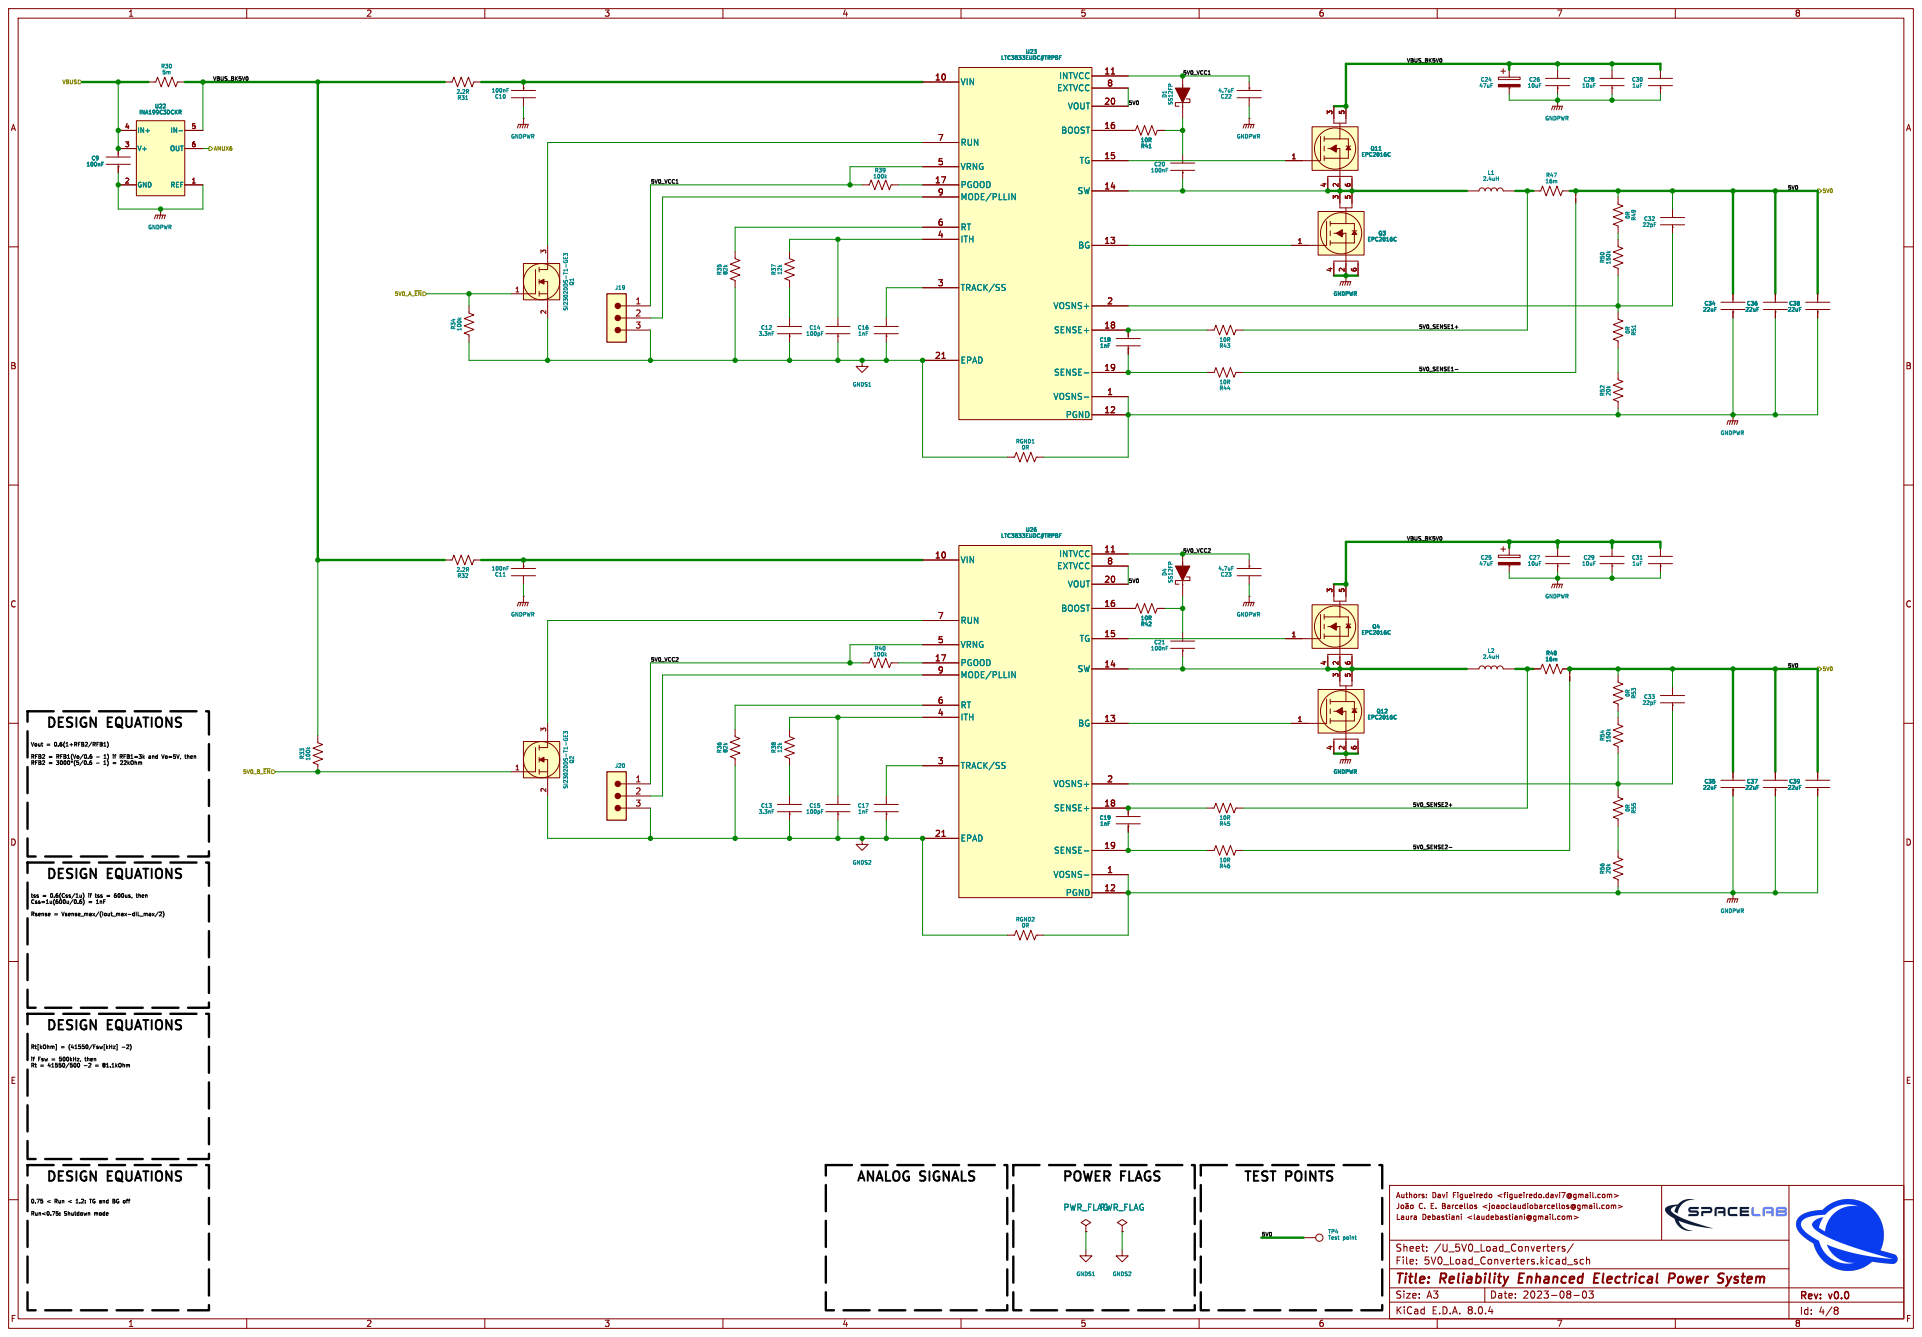
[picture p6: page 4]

Id: 4/8 Title: Reliability Enhanced Electrical Power System

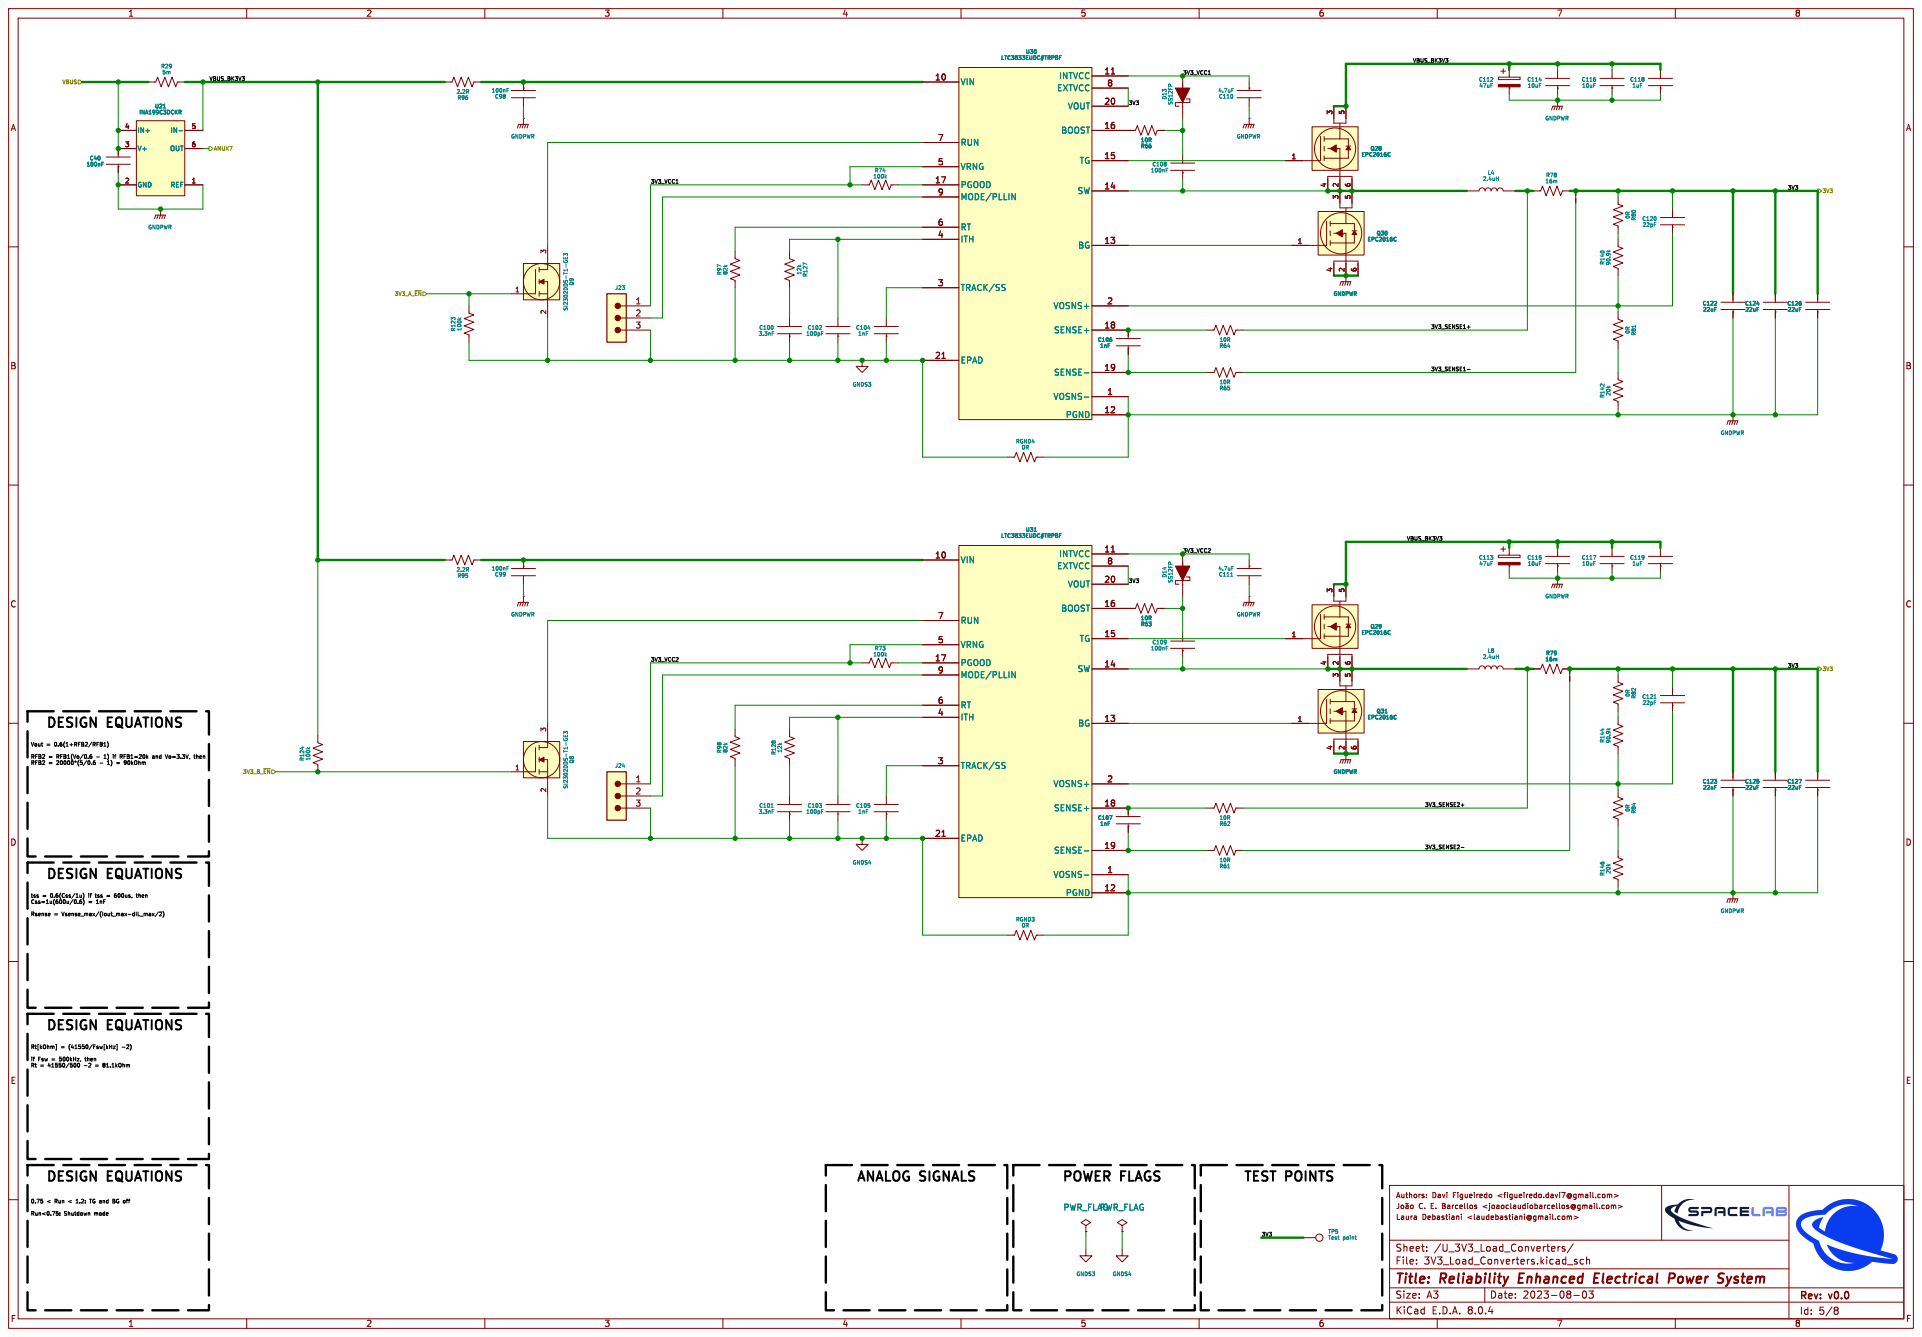
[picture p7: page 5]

Id: 5/8 Title: Reliability Enhanced Electrical Power System

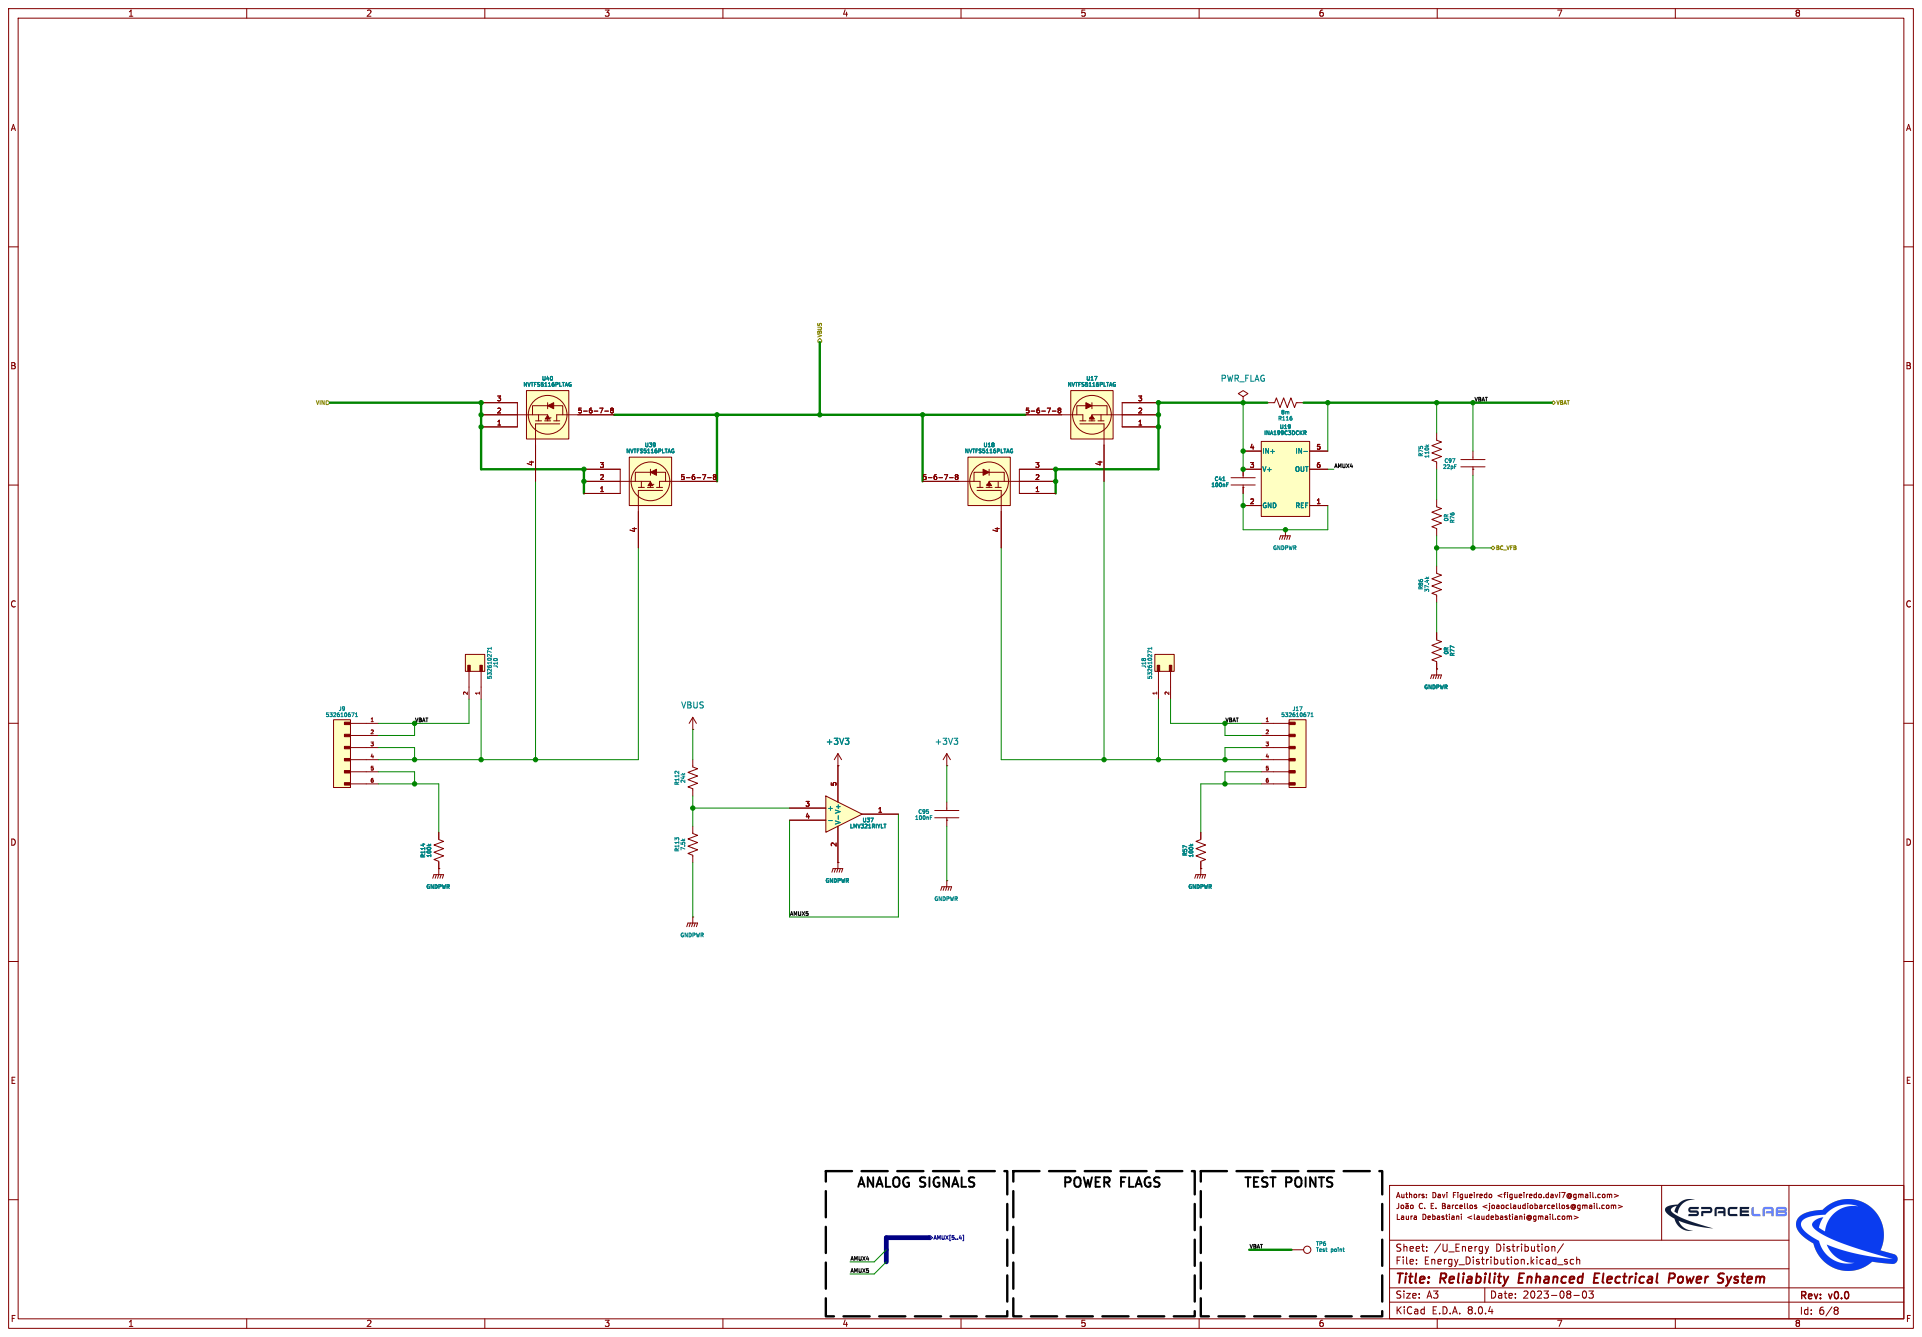
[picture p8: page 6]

Id: 6/8 Title: Reliability Enhanced Electrical Power System

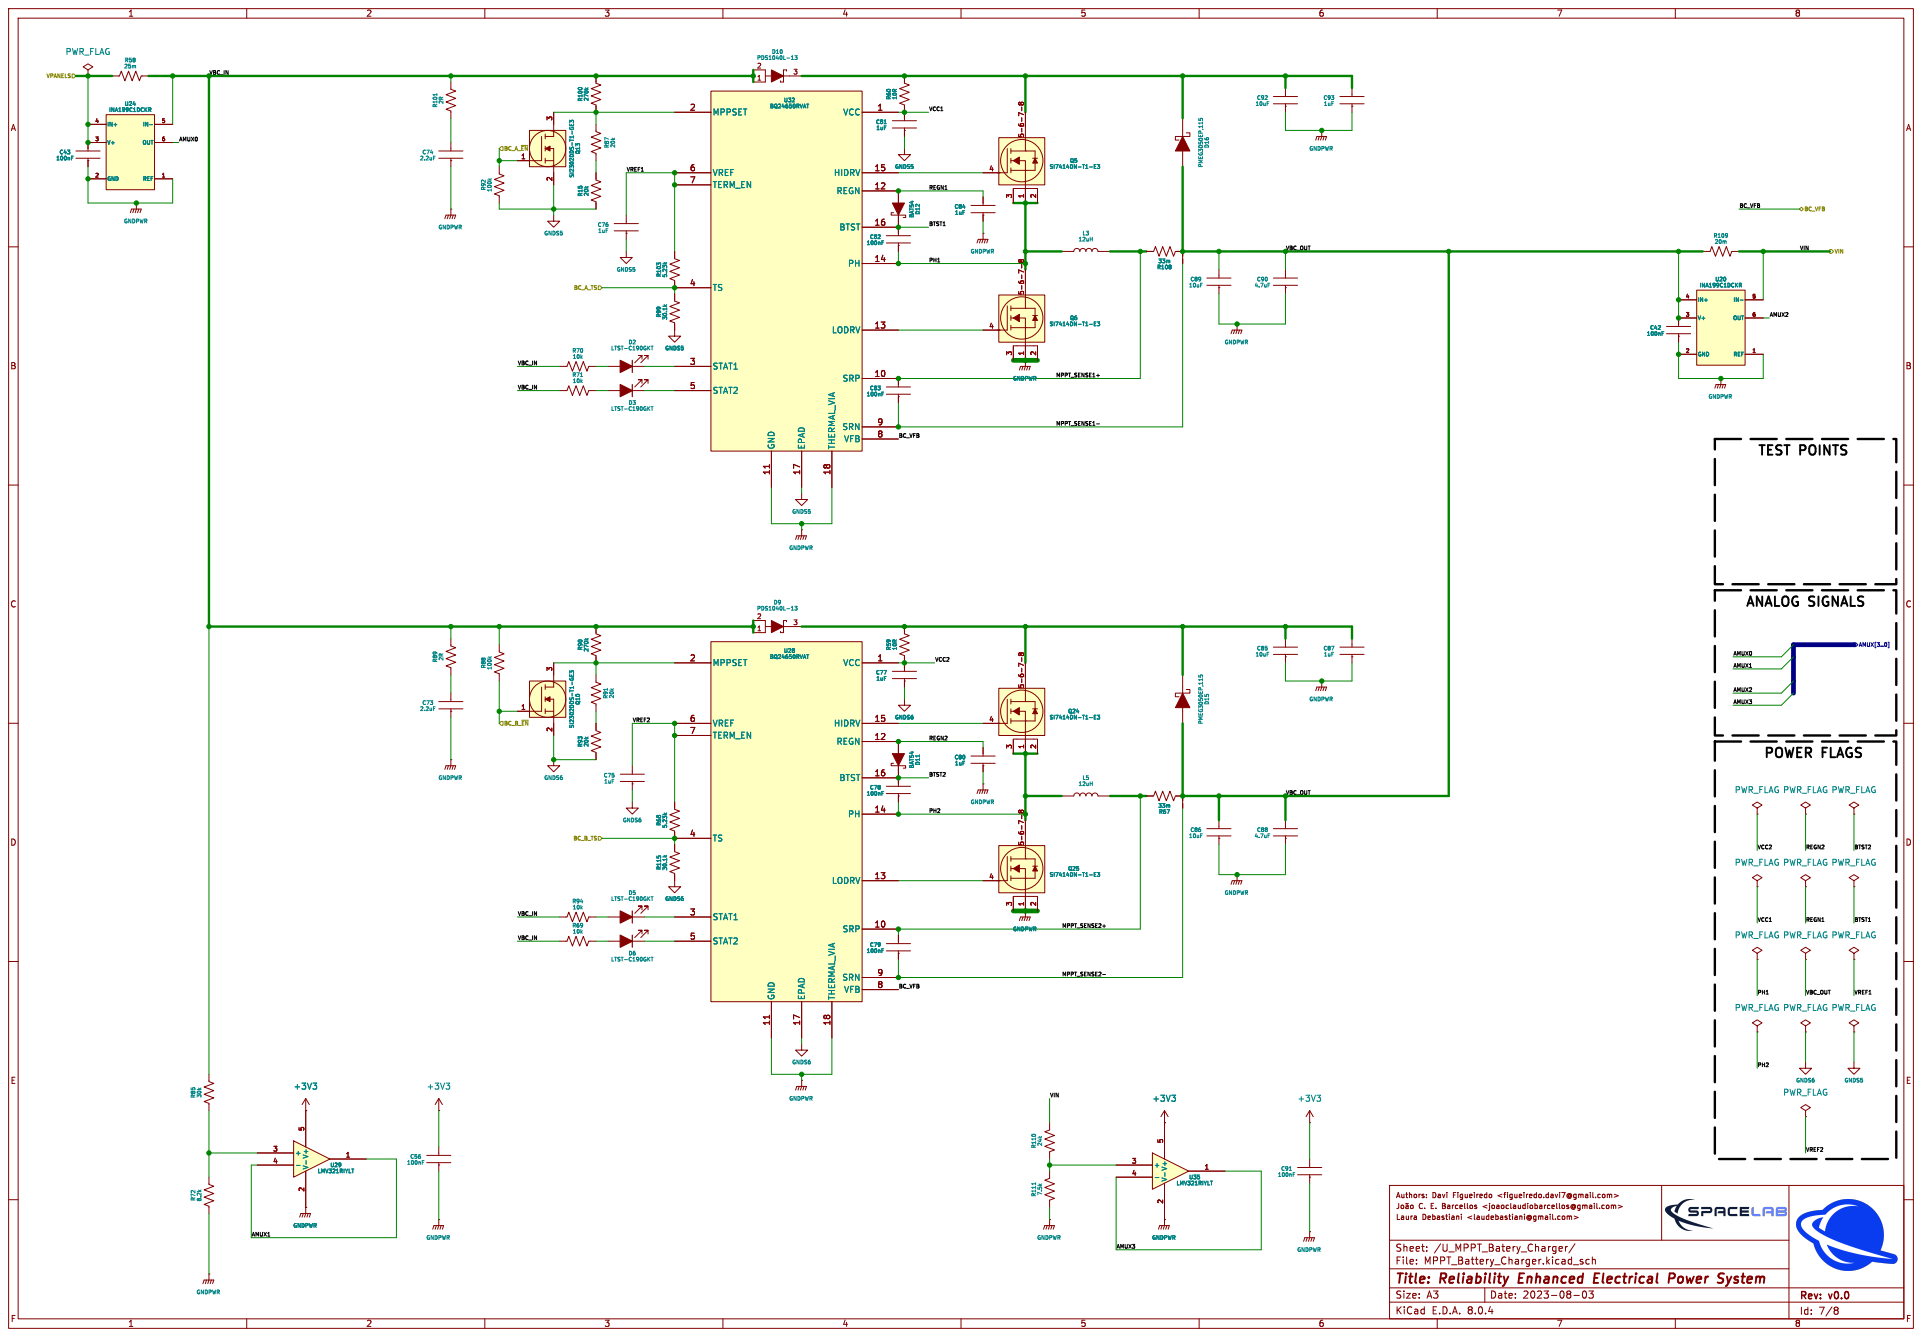
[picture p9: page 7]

Id: 7/8 Title: Reliability Enhanced Electrical Power System

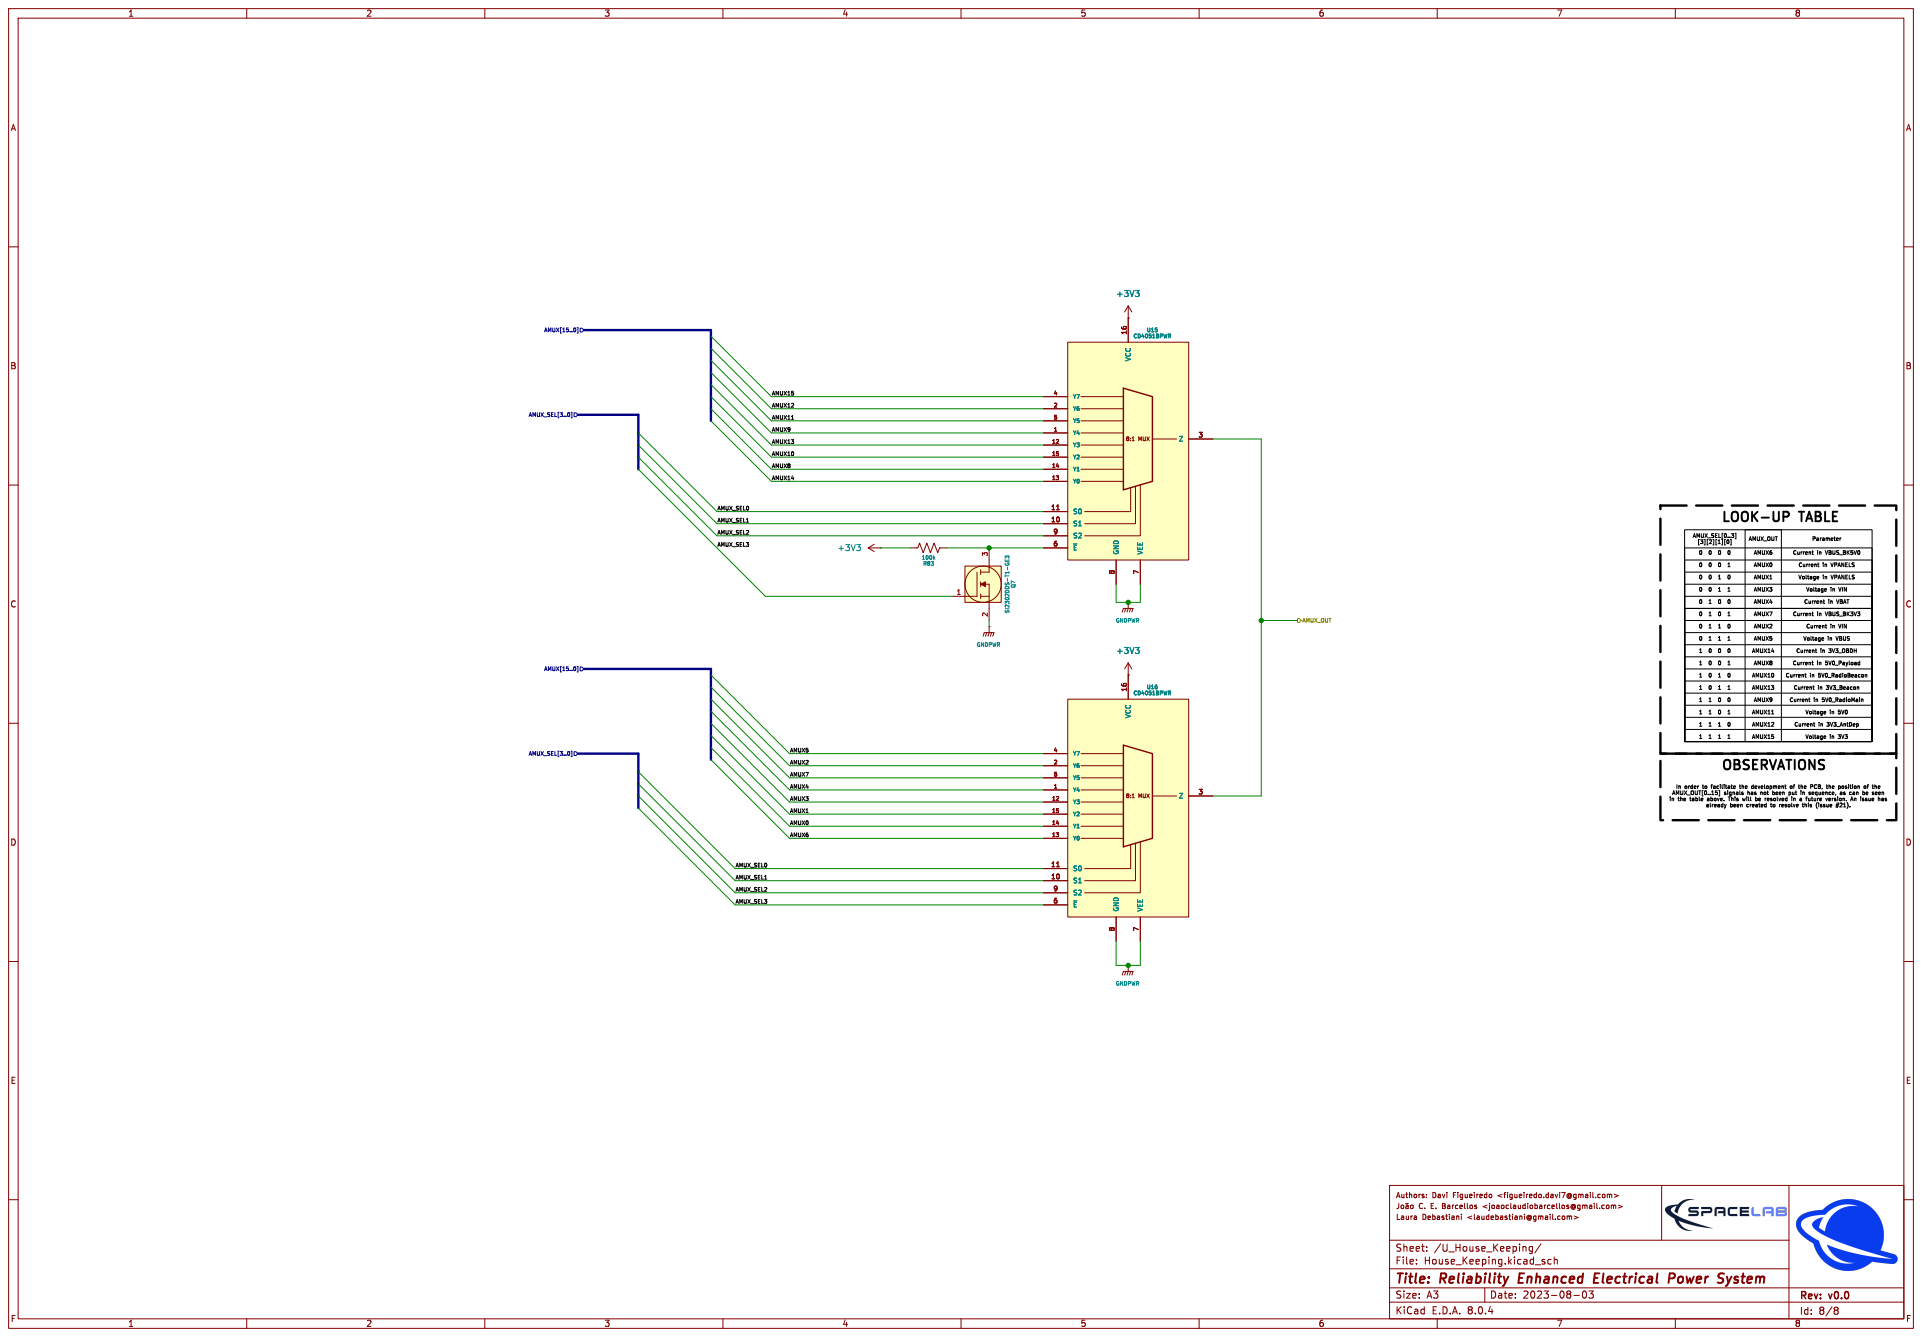
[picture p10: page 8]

Id: 8/8 Title: Reliability Enhanced Electrical Power System

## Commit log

2024-09-05 fix: update the project structure, components and output files
    Fix footprints of some polarized components
    Add 3D models for resistors, capacitors, and more
    Generate the first version of the BOM, schematics, and PCB illustrations
    Add bypass resistors to two power buses for testing purpose
    Add specific folders for outputs and sources to organize project structure in the repository
    Update the README file
    [3V3_Load_Converters.kicad_sch, 3V3_Load_Switches.kicad_sch, 5V0_Load_Converters.kicad_sch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]
2024-10-03 style(figures): update the output figures of the board
